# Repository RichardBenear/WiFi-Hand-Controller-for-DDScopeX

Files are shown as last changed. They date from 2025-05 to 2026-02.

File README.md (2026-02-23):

# --- WiFi Display ---
## aka: TFT Screen Mirror
## aka: WiFi Hand Controller

### Author: Richard Benear  
### Last Modified: June 23, 2025

## Overview

This project adds a **WiFi-based TFT Screen Mirror** for telescope control to the existing DDScopeX telescope. The primary motivation was to control the telescope from an **iPhone** while retaining access to the existing TFT display screens. There are 17 different screens for controlling the DDScopeX which include astronomical catalogs and the Motor Control screen.

Both WiFi Station (STA) and Access Point (AP) modes are supported.

OnStep already provides a webpage interface, but it uses a separate screen rendering system and communicates using LX200 commands and catalog and motor control support are limited. This project provides a real-time mirror of the **actual TFT screen content** rendered by DDScopeX. In otherwords, what you see on the wired TFT Hand Controller is wirelessly sent to any web page capable device and displayed pixel-for-pixel. Additionally, touch or mouse clicks are sent back to the DDScope controller.

This project was developed in PlatformIO / VS Code IDE. Copy
the `include/secretsTemplate.h` file to `include/secrets.h` and
change the SSID and Password to you own before compiling.

## Architecture

- **ESP32-S3**
  - Add an ESP32-S3 to act as a Wifi Server between the Teensy and the router.

- **Pixel Capture**:  
  - Pixels written to the TFT are "captured" via sofware and written in parallel to an **uncompressed buffer** in **PSRAM** on the Teensy 4.1 microprocessor.
- **Compression**
  - The uncompressed buffer is compressed by the Teensy with either RLE or Deflate (the default).
  
- **Memory**:  
  - A full raw frame is ~307,600 bytes.
  - The Teensy’s `DMAMEM` is limited to 512 KB, which is insufficient to hold both uncompressed and compressed images.
  - Therefore, an **8 MB PSRAM module** was added to the Teensy board.

- **Data Transfer**:  
  - Data is sent via **USB Host** on the Teensy 4.1 to the **ESP32-S3’s USB Device** port.
  - Earlier trial versions used a **1 Mbaud UART** connection to an ESP32-C3, but serial data drops due to overruns and noise made this unreliable.
  - USB provides a much **cleaner and more stable** communication channel.
  - Software-based flow control using RTS/CTS was considered but ultimately not required with USB.

- **Memory Optimization**:  
  - To fit the USB stack/library into the base Teensy RAM, large 2D arrays from the Custom Catalog were moved into `EXTMEM`.

## Compression

Various image compression strategies were tested to reduce transfer size:

| Method | Typical Size | Ratio  | Notes |
|---|---|---|---|
| **Uncompressed** | ~307,600 B | 1:1 | Full 320x480 16-bit image |
| **RLE** | ~70–90 KB | ~4:1 | OK compression, simple implementation |
| **LZ4** | ~25–43 KB | ~7:1 | Fast and reliable |
| **Deflate** | ~9 KB | ~35:1  | **Best performance** with acceptable compression size |
| **Difference** | Smallest | varies | Very compact but complex and less reliable |

## Performance

- **Update Rate**:  
  - The main TFT updates at **1 second intervals**.
  - The WiFi mirror display updates at the same rate.
  --The WiFi touch or mouse clicks have an update of 250 msec on the Teensy, although other tasks will delay the response sometimes.

- **Transfer Time**:  
  - With USB at **12 Mbit/sec**, a Deflate-compressed frame (~9 KB) transfers in **~70 ms**.

- **Default Compression**:  
  - **Deflate** is used by default due to its excellent size reduction and fast decompression.

## USB Connection ##
  - There are state machines on the Teensy and ESP32-S3 to handshake and synchronize the USB connection.
  - A WebSocket is used to send the compressed binary data to the Web Page where it is decompressed and rendered.

## Summary

This implementation offers a robust and efficient method for mirroring a Teensy-controlled TFT screen over WiFi using an ESP32-S3 and USB communication. The Deflate compression algorithm ensures minimal latency and efficient use of bandwidth while maintaining visual fidelity.

## Book: BUILD A DIRECT DRIVE TELESCOPE: A Comprehensive Guide
Book Available on Amazon [Here](https://a.co/d/0cUrQWGB) 

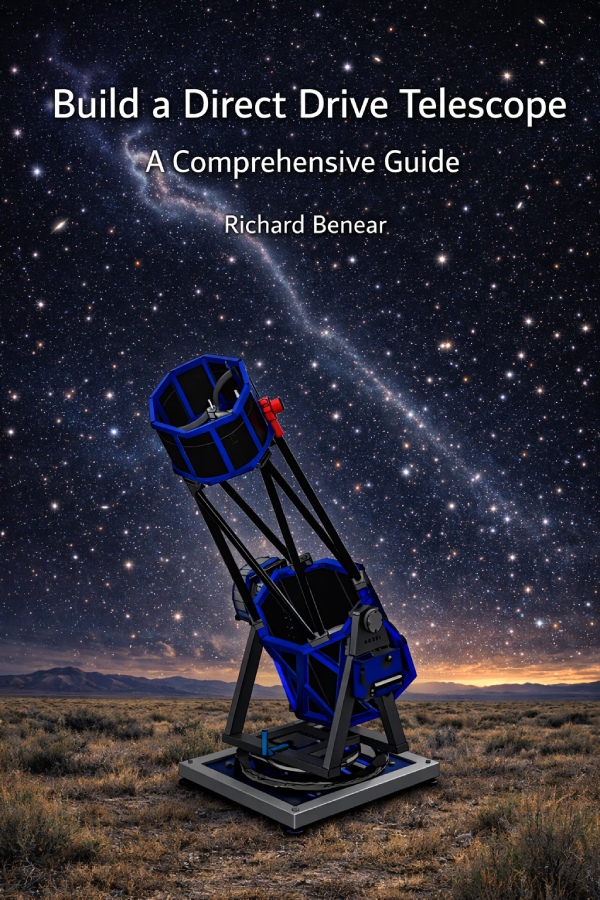
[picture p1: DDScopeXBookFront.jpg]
DDScopeX Book Front


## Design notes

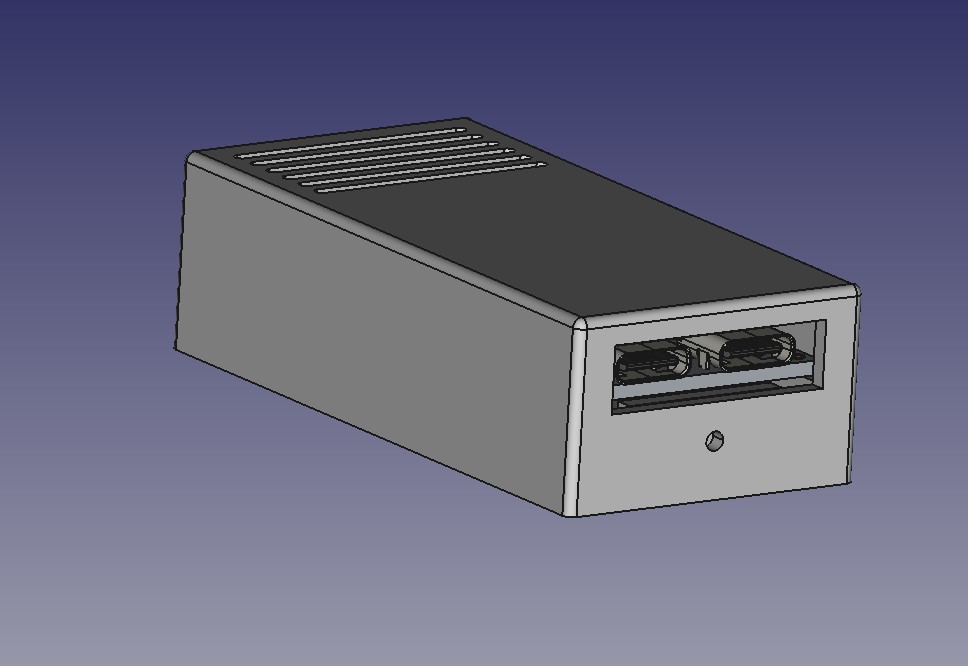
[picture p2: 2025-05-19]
case.jpg

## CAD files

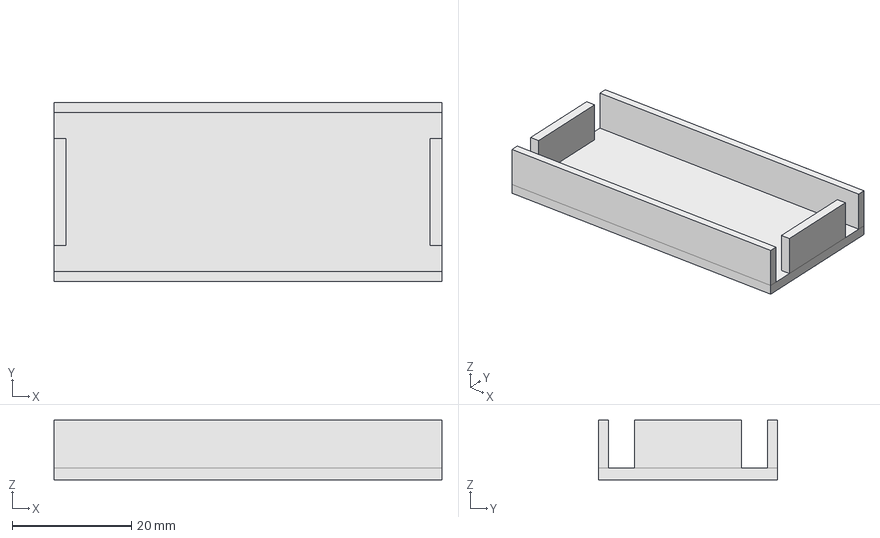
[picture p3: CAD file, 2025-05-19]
WiFiHandControllerCase-Base.step
65.0 x 30.0 x 10.0 mm

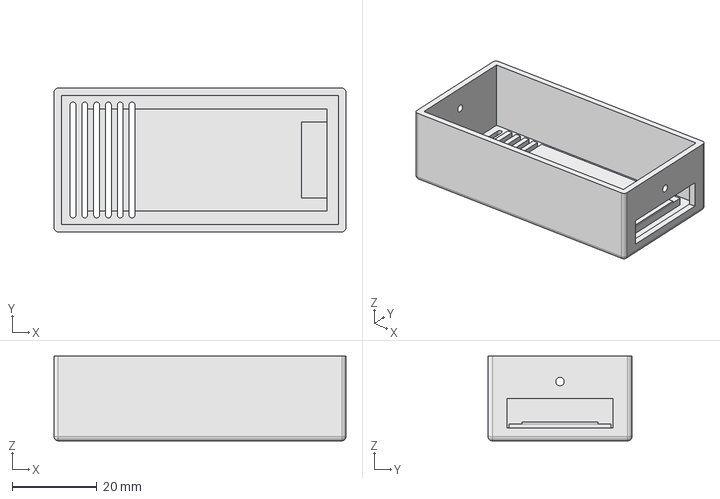
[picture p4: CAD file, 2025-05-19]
WiFiHandControllerCase-Top.step
69.0 x 34.0 x 20.0 mm

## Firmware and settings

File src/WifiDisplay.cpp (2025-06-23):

// ===============================================
// ======== WiFi Screen Mirror for DDScope =======
// ===============================================
// WifiDisplay.cpp
//
// Processor is an ESP32-S3 connected via USB to the Teensy4.1 running DDScopeX code
// 
// See rights and use declaration in License.h
//
// **** by Richard Benear 5/21/2025 ****
//
#include <Arduino.h>
#include <ArduinoJson.h>
#include <AsyncTCP.h>
#include <ESPAsyncWebServer.h>
#include <WiFi.h>
#include <WiFiServer.h>
#include "esp_wifi.h"
#include <esp_heap_caps.h>  // Needed for PSRAM allocation
#include "SPIFFS.h"
#include "esp32/spiram.h"
#include "../include/secrets.h"

#define SERIAL_TEENSY Serial  // USB port
#define SERIAL_DEBUG Serial0

#define FRAME_TYPE_RAW 0x00
#define FRAME_TYPE_RLE 0x01
#define FRAME_TYPE_DEF 0x04

#define FRAME_MAX_SIZE 307200  // For uncompressed 320 x 480 RGB565
#define TEENSY_ACK_TIMEOUT 300

#define HEADER_SIZE 5  // 1 byte type + 4 bytes size
#define FRAME_TOTAL_SIZE (FRAME_MAX_SIZE + HEADER_SIZE)


#define WIFI_DISPLAY_AP_SSID  "WIFI-DISPLAY-ESP32"
#define WIFI_DISPLAY_AP_PASSWORD        "password"
#define WIFI_DISPLAY_AP_IP_ADDR      {192,168,4,2} 
#define WIFI_DISPLAY_AP_GW_ADDR      {192,168,4,2}

AsyncWebServer server(80);
AsyncWebSocket ws("/ws");  // WebSocket endpoint

WiFiServer lx200Server(4030);
WiFiClient lx200Client;

uint32_t frameSize = 0;
size_t bytesRead = 0;
uint8_t *fullFrameBuffer = nullptr;

enum EspState {
  SEND_IP,
  SEND_CONNECTED_STATUS,
  WAIT_FOR_CONNECTED_ACK,
  WAIT_FOR_FRAME
};

EspState espState = SEND_IP;

static String lx200Cmd = "";

volatile bool clientConnected = false;
volatile bool enableProcessFrame = false;
volatile bool touchDetected = false;
int touchX = 0;
int touchY = 0;

bool hasValidRADecCache = false;

String cachedRA = "00:00:00#";
String cachedDec = "+00*00:00#";
unsigned long lastRADecUpdate = 0;

volatile bool lockSerialTeensy = false;
portMUX_TYPE teensySerialMux = portMUX_INITIALIZER_UNLOCKED;

// wrapper functions for mutex
void sendToTeensyByte(uint8_t b) {
  portENTER_CRITICAL(&teensySerialMux);
  SERIAL_TEENSY.write(b);
  portEXIT_CRITICAL(&teensySerialMux);
}

void sendToTeensyBytes(const uint8_t* data, size_t len) {
  for (size_t i = 0; i < len; ++i) {
    portENTER_CRITICAL(&teensySerialMux);
    SERIAL_TEENSY.write(data[i]);
    portEXIT_CRITICAL(&teensySerialMux);
  }
}

void sendToTeensyString(const String& s) {
  portENTER_CRITICAL(&teensySerialMux);
  SERIAL_TEENSY.print(s);
  portEXIT_CRITICAL(&teensySerialMux);
}

void sendToTeensyFlush() {
  portENTER_CRITICAL(&teensySerialMux);
  SERIAL_TEENSY.flush();
  portEXIT_CRITICAL(&teensySerialMux);
}

// Send any Touch event to Teensy
// Touch event is asynchronous from the loop().
void sendTouchCoord() {
  if (touchDetected) {

    // Send to Teensy over USB CDC
    SERIAL_TEENSY.write('T');                  // Touch event marker
    SERIAL_TEENSY.write((uint8_t)(touchX >> 8));    // x high byte
    SERIAL_TEENSY.write((uint8_t)(touchX & 0xFF));  // x low byte
    SERIAL_TEENSY.write((uint8_t)(touchY >> 8));    // y high byte
    SERIAL_TEENSY.write((uint8_t)(touchY & 0xFF));  // y low byte
    touchDetected = false;
    ws.textAll("ack");  // Send acknowledgment back to client
  }
}

// Send the IP address to Teensy
String sendIpToTeensy() {
  IPAddress ip = WiFi.localIP();
  String ipMsg = "IP:" + ip.toString() + "\n";
  SERIAL_TEENSY.print(ipMsg);
  SERIAL_TEENSY.flush();
  return ipMsg;
}

// ==============================================================
// Receive the Frame Header and compressed Frame data from Teensy
// ==============================================================
// The metadata byte sent to the WebSocket client:
// 0x00 = Raw
// 0x01 = Compressed RLE
// 0x04 = Compressed Deflate
void processFrame() {
  if (!enableProcessFrame) return;
  frameSize = 0;
  bytesRead = 0;

  // STEP 1: Wait for and verify the sync byte
  if (SERIAL_TEENSY.peek() == 'Z') {
    SERIAL_TEENSY.read();
    SERIAL_TEENSY.write(0x06);  // ACK
    SERIAL_TEENSY.flush();
    //SERIAL_DEBUG.println("Got 'Z'");
  } else {
    //SERIAL_DEBUG.printf("Unexpected byte: 0x%02X (expected 'Z')\n", SERIAL_TEENSY.peek());
    //SERIAL_TEENSY.read();  // Discard it
    return;
  }
  delay(3);
  //******************************************************* */
  if (SERIAL_TEENSY.available() >= HEADER_SIZE) {
    // Read 5-byte header
    SERIAL_TEENSY.readBytes(fullFrameBuffer, HEADER_SIZE);

    uint8_t frameType = fullFrameBuffer[0];
    uint32_t frameSize = fullFrameBuffer[1] | (fullFrameBuffer[2] << 8) |
                         (fullFrameBuffer[3] << 16) |
                         (fullFrameBuffer[4] << 24);

    //SERIAL_DEBUG.printf("Frame type: 0x%02X\n", fullFrameBuffer[0]);
    //SERIAL_DEBUG.printf("Size (%u bytes) as [0x%02X 0x%02X 0x%02X 0x%02X]\n",
    //                    frameSize, fullFrameBuffer[1], fullFrameBuffer[2],
    //                    fullFrameBuffer[3], fullFrameBuffer[4]);

    if (frameSize == 0 || frameSize > FRAME_MAX_SIZE) {
      SERIAL_DEBUG.printf("Invalid frame size: %u\n", frameSize);
      espState = SEND_IP;
      return;
    }
   

    // Wait until full frame arrives
    size_t bytesToRead = frameSize;
    uint8_t *payloadPtr = fullFrameBuffer + HEADER_SIZE;
    unsigned long startWaitPayload = millis();

    while (bytesToRead > 0) {
      int availableBytes = SERIAL_TEENSY.available();
      if (availableBytes > 0) {
        int chunk = min((int)bytesToRead, availableBytes);
        int bytesReadNow = SERIAL_TEENSY.readBytes(payloadPtr, chunk);
        payloadPtr += bytesReadNow;
        bytesToRead -= bytesReadNow;
        delayMicroseconds(100);
      } else {
        if (millis() - startWaitPayload > 300) {
          SERIAL_DEBUG.println("Timeout waiting for frame payload");
          return;
        }
        delayMicroseconds(200); //  a yield to USB 
      }
    }
    // Send compressed data over WebSocket
    ws.binaryAll(fullFrameBuffer, HEADER_SIZE + frameSize);
  }
}

// =========== Frame handshaking Handler ====================
// =========== State Flow Signal Meanings ===================
//  Byte	     Meaning
//   'D'     ESP32S3 sends: Client has disconnected
//   'I'	   ESP32S3 sends: IP address (e.g., I192.168.1.55\n)
//   'K'	   ESP32S3 receives: Teensy acknowledgement
//   'C'	   ESP32S3 sends: Client is connected
//   'K'	   ESP32S3 receives: Teensy acknowledgement
//   'T'     ESP32S3 sends: Touchscreen event
//   'Z'     ESP32S3 receives: Start frame signal from Teensy
void checkFrameState() {
  static bool prevClientConnected = false;

  // Detect Web Client Disconnect (i.e. falling edge)
  if (prevClientConnected && !clientConnected) {
    SERIAL_DEBUG.println("[ESP32] Web client disconnected — sending 'D' to Teensy");
    SERIAL_TEENSY.write('D');
    SERIAL_TEENSY.flush();
    espState = SEND_IP;
  }
  prevClientConnected = clientConnected;
  String wifiStaIpStr = "";

  switch (espState) {
    case SEND_IP:
      enableProcessFrame = false;
      //SERIAL_DEBUG.println("[ESP32] Sending IP to Teensy");
      wifiStaIpStr = sendIpToTeensy();
      delay(1);
      if (SERIAL_TEENSY.available()) {
        char incoming = SERIAL_TEENSY.read();
        if (incoming == 'K') {
          SERIAL_DEBUG.println("[ESP32] Received IP ACK");
          SERIAL_DEBUG.print("IP Address: ");
          SERIAL_DEBUG.println(wifiStaIpStr);
          espState = SEND_CONNECTED_STATUS;
        }
      }
      break;

    case SEND_CONNECTED_STATUS:
      if (clientConnected) {
        SERIAL_DEBUG.println("[ESP32] Sending 'C'");
        SERIAL_TEENSY.write('C');
        espState = WAIT_FOR_CONNECTED_ACK;
      }
      break;

    case WAIT_FOR_CONNECTED_ACK:
       if (SERIAL_TEENSY.available()) {
        char incoming = SERIAL_TEENSY.read();
        if (incoming == 'K') {
          SERIAL_DEBUG.println("[ESP32] Teensy ACK connected");
          enableProcessFrame = true;  // Start the Frame Processing
          SERIAL_DEBUG.println("Setting enableProcessFrame = true");
          espState = WAIT_FOR_FRAME;
        }
      }
      break;

    case WAIT_FOR_FRAME:
      processFrame();
      break;

    default:
      //espState = SEND_IP;
      break;
  }
}

// ===============================================
// =================== SETUP =====================
// ===============================================
void setup() {
  delay(2000);

  SERIAL_DEBUG.begin(115200);
  SERIAL_DEBUG.println("Debug port started");

  // USB port begin...probably already initialized, but?
  SERIAL_TEENSY.begin(1000000); // baud rate doesn't affect anything
  delay(1000);

  if (!psramFound()) {
    SERIAL_DEBUG.println("PSRAM not found!");
    while (true);  // Halt
  }
  SERIAL_DEBUG.printf("PSRAM Size: %u bytes\n", ESP.getPsramSize());

  // Need SPIFFS because we are serving the HTML
  if (!SPIFFS.begin(true)) {
    SERIAL_DEBUG.println("Failed to mount SPIFFS");
    return;
  }
  SERIAL_DEBUG.println("SPIFFS mounted");

  // Single receive buffer in PSRAM
  fullFrameBuffer = (uint8_t *)ps_malloc(FRAME_TOTAL_SIZE);
  if (!fullFrameBuffer) {
    Serial.println("ERROR: PSRAM malloc failed for fullFrameBuffer!");
    while (true);  // Halt here
  }
  delay(10);

  // Using Dual mode Wifi
  WiFi.mode(WIFI_AP_STA);

  // Start WiFi
  WiFi.begin(WIFI_SSID, WIFI_PASSWORD);
  while (WiFi.status() != WL_CONNECTED) {
    delay(500);
    SERIAL_DEBUG.print(".");
  }
  SERIAL_DEBUG.print("\nWiFi connected. IP Address: ");
  SERIAL_DEBUG.println(WiFi.localIP());

  delay(10);

  // Start AP (Access Point) mode
  WiFi.setSleep(false);  // Optional, prevents disconnects

  // Set static AP IP
  WiFi.softAPConfig(
    IPAddress(WIFI_DISPLAY_AP_IP_ADDR),
    IPAddress(WIFI_DISPLAY_AP_GW_ADDR),
    IPAddress(255, 255, 255, 0)
  );

  // Now start AP :  Channel 1, hidden SSID off, max 1 client
  bool apStarted = WiFi.softAP(WIFI_DISPLAY_AP_SSID, WIFI_DISPLAY_AP_PASSWORD, 1, 0, 1);
  if (!apStarted) {
    SERIAL_DEBUG.println("Failed to start Access Point!");
  } else {
    SERIAL_DEBUG.println("Access Point started");
  }

  // Print AP IP address (this returns the softAP IP)
  IPAddress apIp = WiFi.softAPIP();
  SERIAL_DEBUG.print("AP IP Address: ");
  SERIAL_DEBUG.println(apIp);

  // Serve HTML file
  server.on("/", HTTP_GET, [](AsyncWebServerRequest *request) {
    if (SPIFFS.exists("/WifiDisplay.html")) {
      request->send(SPIFFS, "/WifiDisplay.html", "text/html");
    } else {
      request->send(404, "text/plain", "File not found");
    }
  });
  server.serveStatic("/", SPIFFS, "/");

  // WebSocket events
  ws.onEvent([](AsyncWebSocket *server, AsyncWebSocketClient *client,
                AwsEventType type, void *arg, uint8_t *data, size_t len) {
    if (type == WS_EVT_CONNECT) {
      SERIAL_DEBUG.println("client connected");
      clientConnected = true;
    } else if (type == WS_EVT_DISCONNECT) {
      SERIAL_DEBUG.println("client not connected");
      clientConnected = false;
    } else if (type == WS_EVT_DATA) {
      AwsFrameInfo *info = (AwsFrameInfo *)arg;
      if (info->final && info->index == 0 && info->len == len &&
          info->opcode == WS_TEXT) {
        data[len] = 0;  // null-terminate string

        // SERIAL_DEBUG.printf("WebSocket received: %s\n", (char *)data);

        // Parse JSON
        JsonDocument doc;
        DeserializationError error = deserializeJson(doc, data, len);
        if (error) {
          SERIAL_DEBUG.println("Failed to parse JSON");
          return;
        }

        touchDetected = true;

        if (doc["type"] == "TOUCH") {
          touchX = doc["x"];
          touchY = doc["y"];
          // SERIAL_DEBUG.printf("TOUCH: x=%d, y=%d\n", x, y);
          SERIAL_DEBUG.println("TOUCH");
        }
      }
    }
  });
  server.addHandler(&ws);

  server.begin();
  SERIAL_DEBUG.println("Server started");
  SERIAL_DEBUG.printf("Free heap: %u, PSRAM: %u\n", ESP.getFreeHeap(),
                      ESP.getFreePsram());

  SERIAL_TEENSY.write('D');
  SERIAL_TEENSY.flush();
  clientConnected = false;
}

//====================================================
// ====================== LOOP =======================
//====================================================
void loop() {
  
  checkFrameState();
  sendTouchCoord();
  yield();

}
